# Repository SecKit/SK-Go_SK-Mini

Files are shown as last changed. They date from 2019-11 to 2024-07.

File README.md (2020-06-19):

# SK-Go² All-Metal CoreXY 3D Printer

Website

https://seckit3dp.design/

Join SecKit's FaceBook group for owner's discussion and latest update

https://www.facebook.com/groups/SecKitCoreXY3DP/

YouTube

https://www.youtube.com/channel/UCJUHiJfgDE5aeqbk4iZBPHA/videos

FaceBook Page

https://www.facebook.com/seckit.3dp

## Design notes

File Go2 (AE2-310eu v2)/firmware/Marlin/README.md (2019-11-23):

**How to re-flash firmware**

1. Put a corresponding binary into a TF card (micro SD). The 128MB TF comes with SKR v1.3 which must be **FAT16** formatted, other larger TF can be FAT32.
2. Rename the file as **firmware.bin**
3. Put the TF card into the slot on SKR v1.3
4. Reboot and it will re-flash. If success, the firmware.bin should have been renamed as FIRMWARE.CUR.

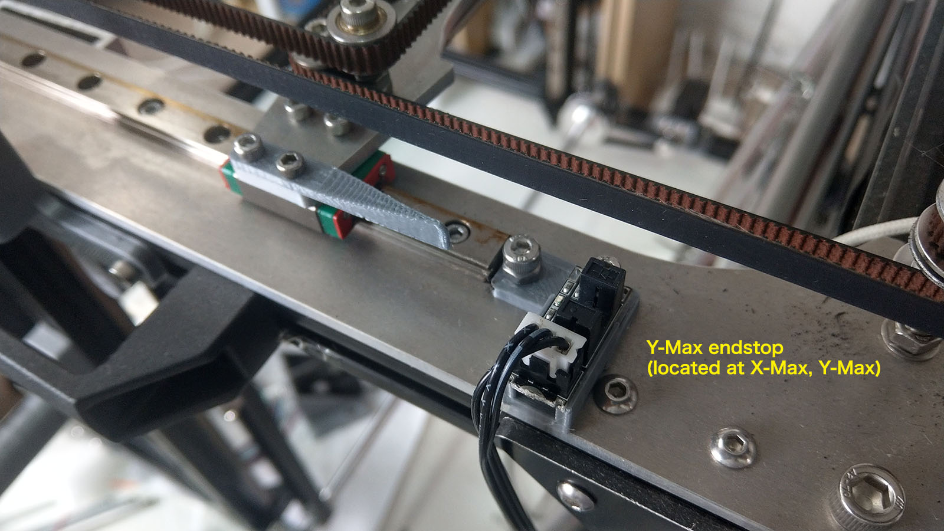
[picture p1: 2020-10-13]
Go2 (AE2-310eu v2)/printed parts STL/3. Optional/XY optical endstop mounts/Y-Max endstop.jpg

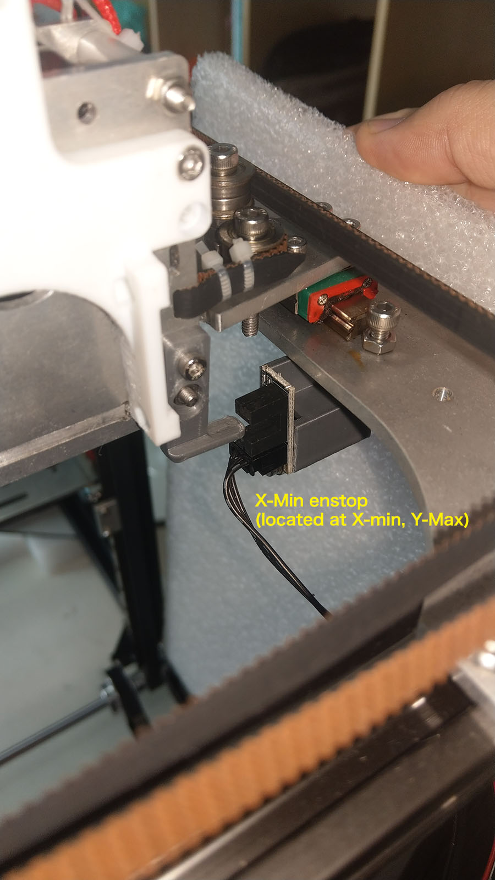
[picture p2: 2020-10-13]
Go2 (AE2-310eu v2)/printed parts STL/3. Optional/XY optical endstop mounts/X-min endstop 2.jpg

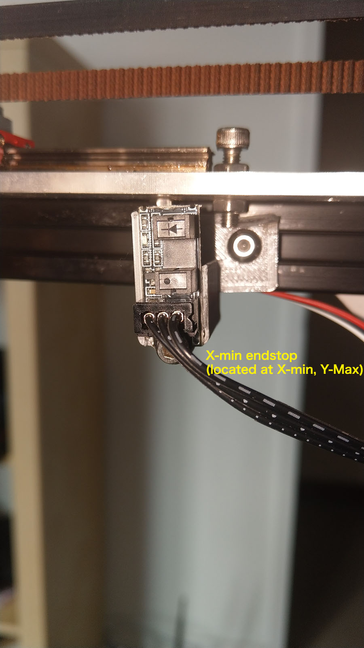
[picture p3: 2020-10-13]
Go2 (AE2-310eu v2)/printed parts STL/3. Optional/XY optical endstop mounts/X-min endstop 1.jpg

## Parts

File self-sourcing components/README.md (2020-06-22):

Self-sourcing components for SK-Go² Foundation & Barebones Kit.

|Category  |Item | #|Electrical req. |Mechanical req. |
|---|:---|-:|:---|:---|
|Power |Meanwell LRS-200-24 PSU | 1|200 or 350 watt, 24V output |4 holes on back panel (PS.)|
|Power |SSR DC-AC | 1|At least 10 amp AC |2 holes on back panel |
|Power |FS-101 fuse box and fuse | 1|6A for 110V. 3A for 220V. |1 hole on back panel |
|Power |Power switch | 1| | |
|Power |Power cord | 1|At least 0.75 mm^2 internal wire |150cm or longer |
|Control |BigTreeTech SKR v1.3. | 1|(or other control board) |4 holes on back panel |
|Control |BigTreeTech TMC2209 | 4|(or other drivers) | |
|Control |12864 LCD | 1|(optional) | |
|Control |JTAG cable for 12864 LCD, 80cm | 2|(optional) |80cm or longer |
|Stepper |NEMA17 1.8° stepper for XYZ | 3|Common NEMA 17 stepper | |
|Stepper |NEMA17 1.8° pancake stepper for E | 1|Common NEMA 17 pancake stepper |max 24mm tall (PPS.) |
|Extruder  |BMG or Hemera extruder | 1| | |
|Fan |4010 fan for driver cooling | 1|24V | |
|Fan |4020 blower for part cooling | 1|24V | |
|Sensor |Lerdge optical endstop, Z-min. | 1|5V | |
|Sensor |Filament runout sensor | 1|(optional) | |
|Accessory |PTFE tube 1.75mm, 80cm | 1| | |
|Accessory |Cable tie |20| | |
|Accessory |Cable management nylon sleeve, wrapper, etc.| 1| | |

PS. Pre-drilled holes are there on the ACM (Aluminum Composite Material) back panel but you can still drill customized holes easily.

PPS. For direct extrusion E stepper should be at most 24mm tall, or it cannot be inserted in between stock extruder plates.

*SecKit will not be responsible for your self-sourcing items.*

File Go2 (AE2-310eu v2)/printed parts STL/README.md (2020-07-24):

SK-Go² can still start it's initial print without these parts. Below are some workarounds if you don't have them printed.

**Assembly guide**

A ruler or caliper that keeps dimensions consistent will work. It's just a convenient tool and you can still complete the building without it.

**Cable pillar**

Temporarily hold wires/cables onto sticks.

**Driver cooling fan mount**

TMC drivers still work without a fan and they auto reduce working current if overheated.

**Part-cooling fan duct**

A desktop fan placed by the printer will work.

**X-min sensorless homing bumper**

It still homes without this bumper, just noisier.

**12864 Display cover**

The display still works without a cover.

**Filament sensor holder**

Temporarily turn sensor off in the display menu, or put a piece of filament in the sensor to emulate filament always exists.

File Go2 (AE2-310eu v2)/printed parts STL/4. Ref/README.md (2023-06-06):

The DXF file of a wider Go1/Go2 X plate.

License: CC BY-NC-SA 4.0

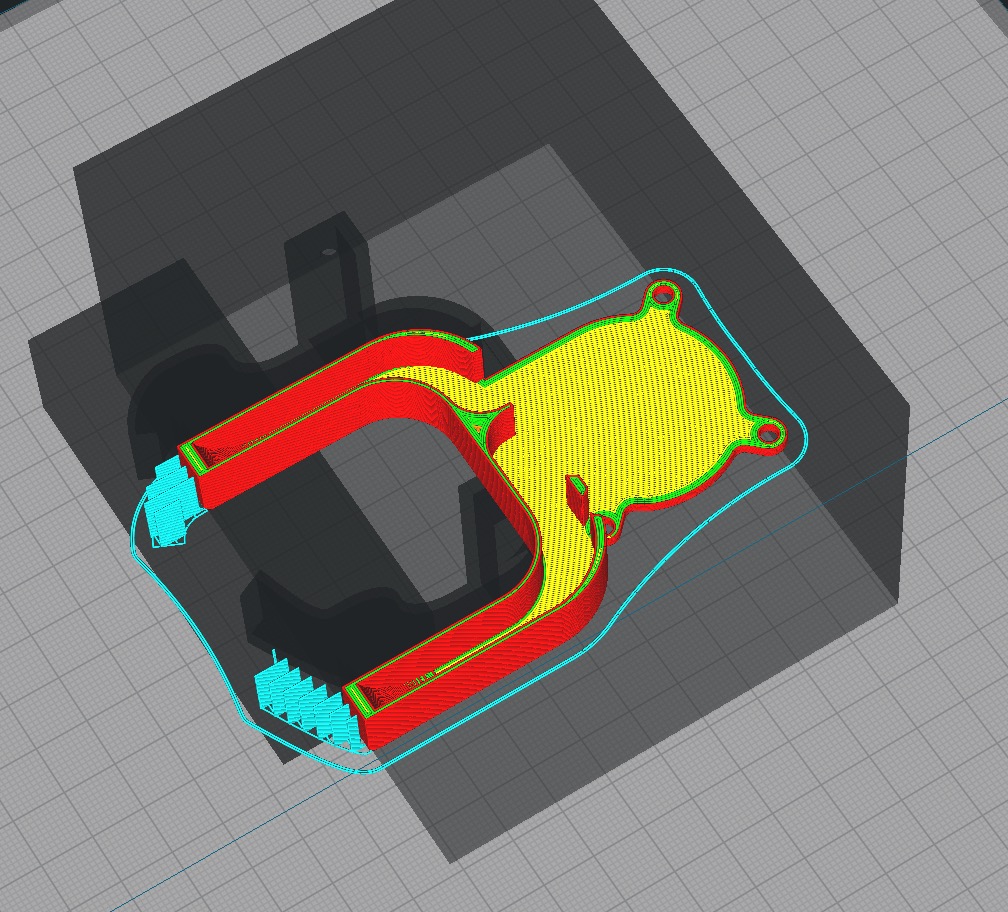
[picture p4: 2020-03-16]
Go2 (AE2-310eu v2)/printed parts STL/2. Recommended/4. Part-cooling fan duct/Direct.v2/pic1.jpg

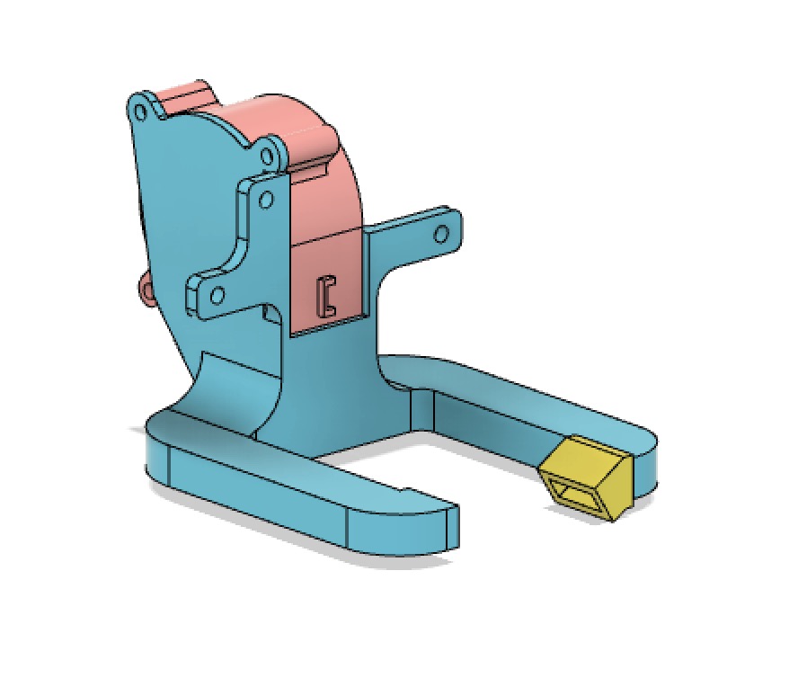
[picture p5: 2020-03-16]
Go2 (AE2-310eu v2)/printed parts STL/3. Optional/E3D Hemera fan duct/pic0.jpg

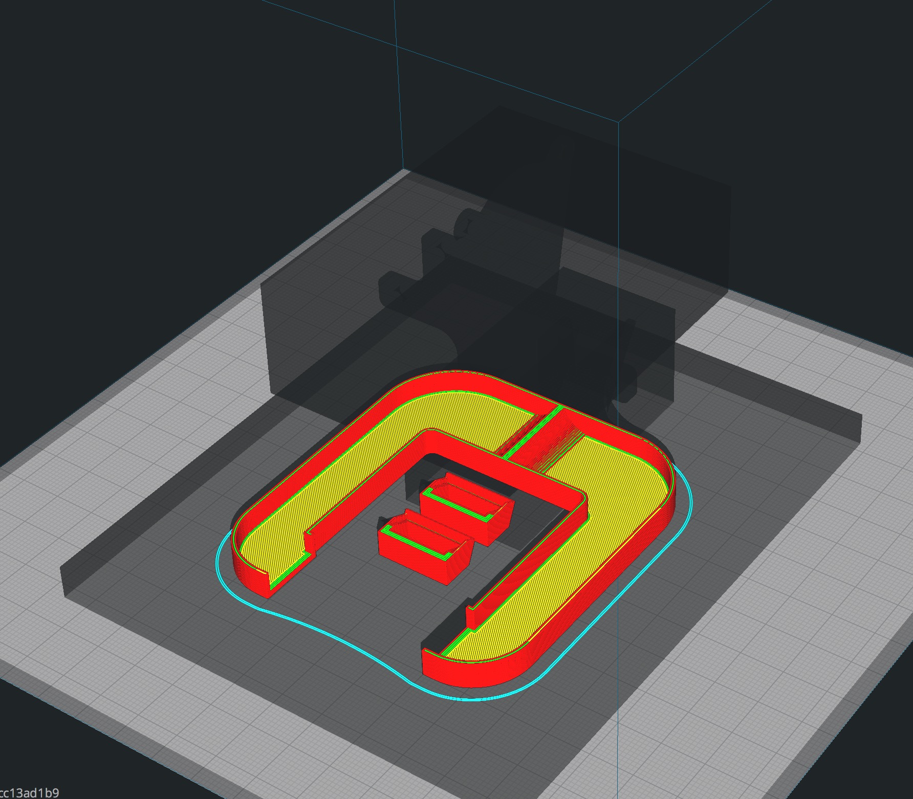
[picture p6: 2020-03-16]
Go2 (AE2-310eu v2)/printed parts STL/3. Optional/E3D Hemera fan duct/pic1.jpg

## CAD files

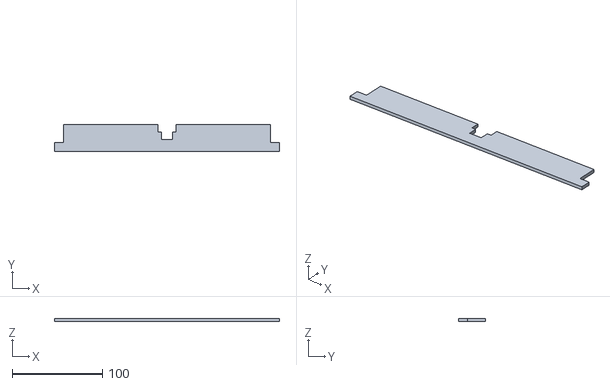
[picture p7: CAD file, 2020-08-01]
Go2 (AE2-310eu v2)/printed parts STL/2. Recommended/1. Assembly guide/SK-Go2 assembly guide - Setup A.stl
250.0 x 29.5 x 3.00

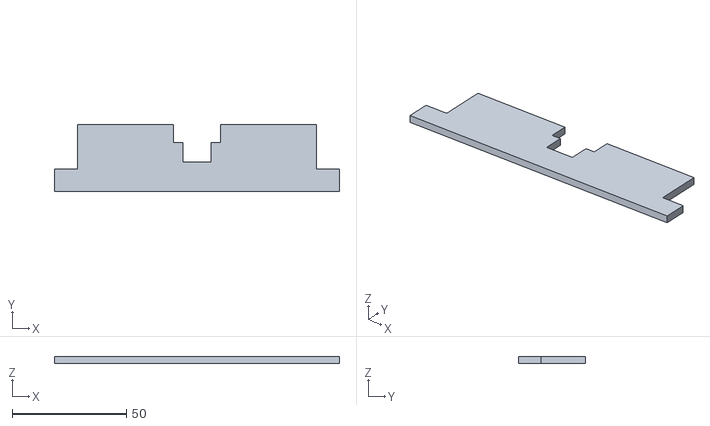
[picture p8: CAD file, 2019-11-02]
Go2 (AE2-310eu v2)/printed parts STL/2. Recommended/1. Assembly guide/SK-Mini assembly guide.stl
125.0 x 29.5 x 3.00

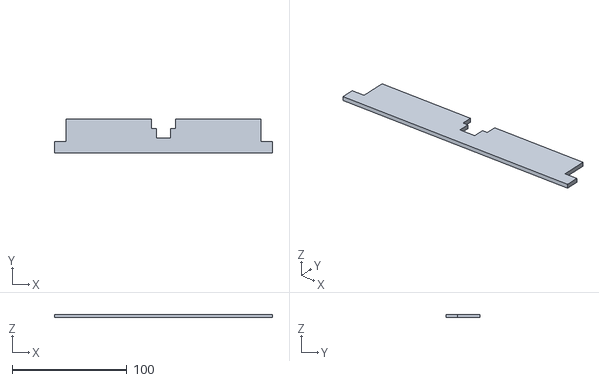
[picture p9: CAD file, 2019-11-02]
Go2 (AE2-310eu v2)/printed parts STL/2. Recommended/1. Assembly guide/SK-Go2 assembly guide - Setup B.stl
190.0 x 29.5 x 3.00

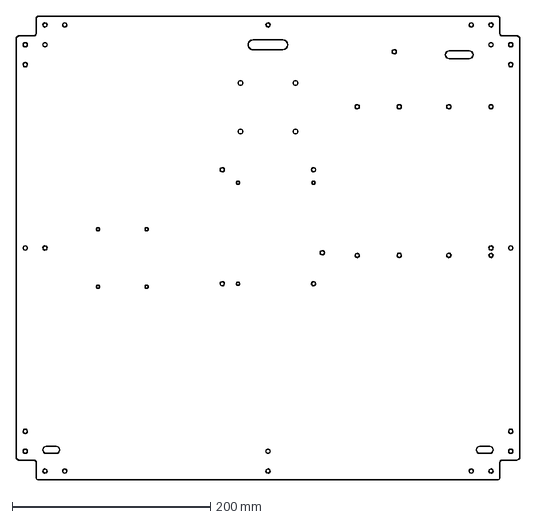
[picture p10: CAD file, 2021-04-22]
frame spec/SK-Go back panel Z350.dxf
507.9 x 468.0 mm

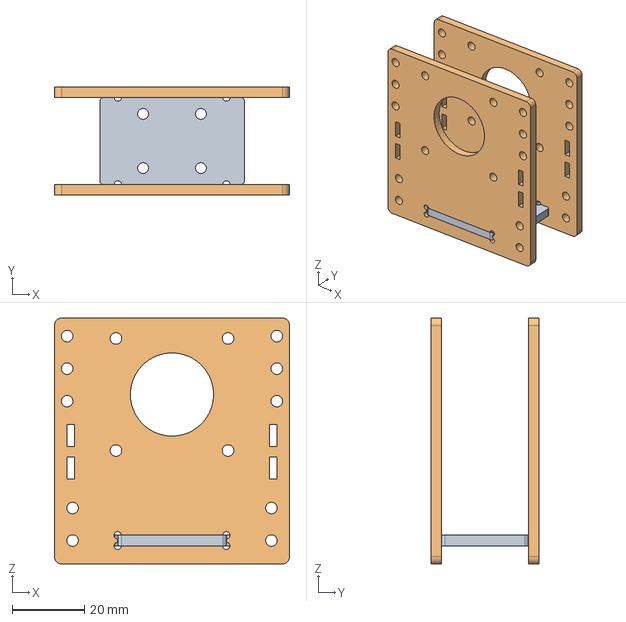
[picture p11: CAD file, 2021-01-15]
Go2 (AE2-310eu v2)/extruder carriage STEP file/SK-Go extruder carriage plates.step
65.0 x 30.0 x 68.0 mm

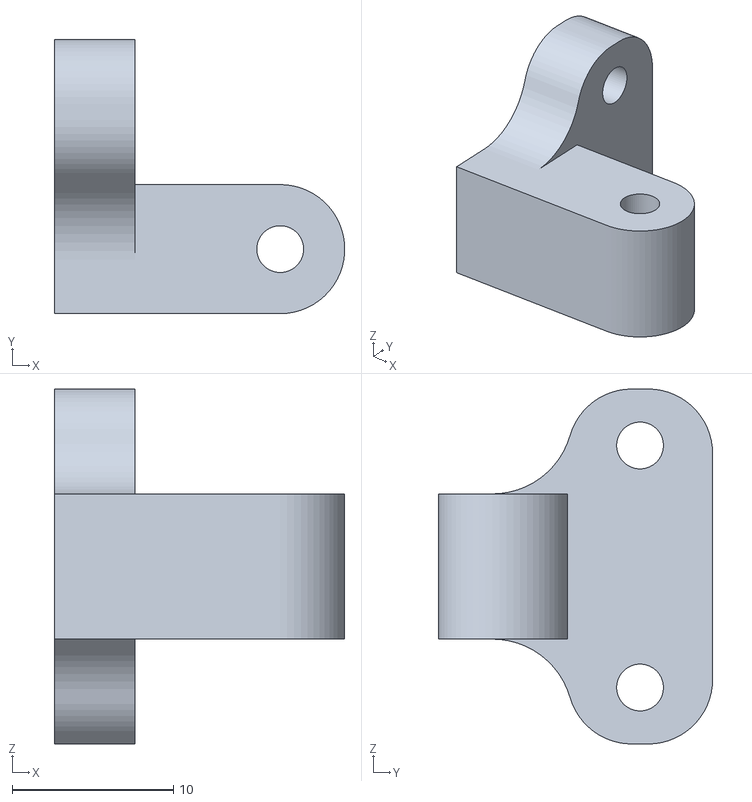
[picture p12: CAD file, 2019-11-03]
Go2 (AE2-310eu v2)/printed parts STL/1. Must/Z endstop mount/Mechanical endstop/Mechanical endstop mount by Michael Laws/SK-Go Z endstrop trigger mount by Michael Laws.stl
18.0 x 17.0 x 22.0

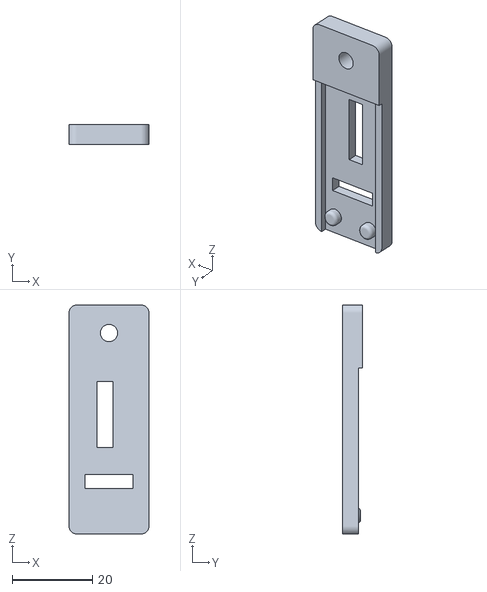
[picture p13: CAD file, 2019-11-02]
Go2 (AE2-310eu v2)/printed parts STL/1. Must/Z endstop mount/Mechanical endstop/Mechanical endstop mount/SK-Go Z endstop mount.stl
20.0 x 5.00 x 57.2

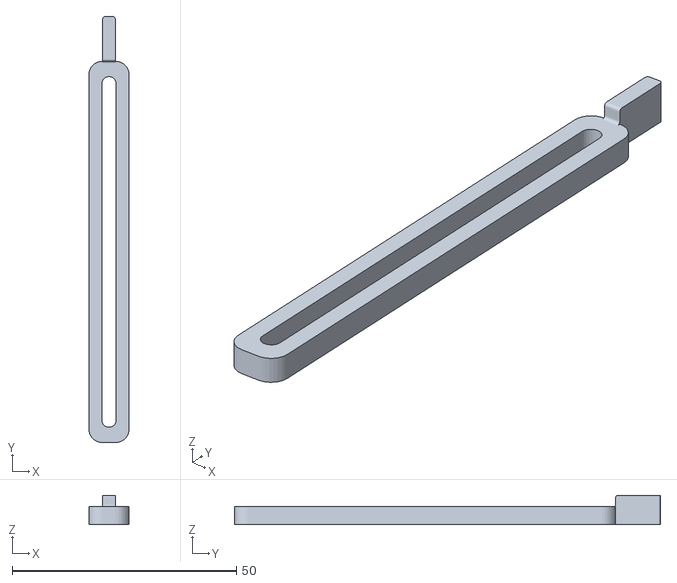
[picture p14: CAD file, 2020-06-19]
Go2 (AE2-310eu v2)/printed parts STL/1. Must/Z endstop mount/Optical endstop/SK-Go Z optical endstop trigger 95mm.stl
9.00 x 95.0 x 6.50

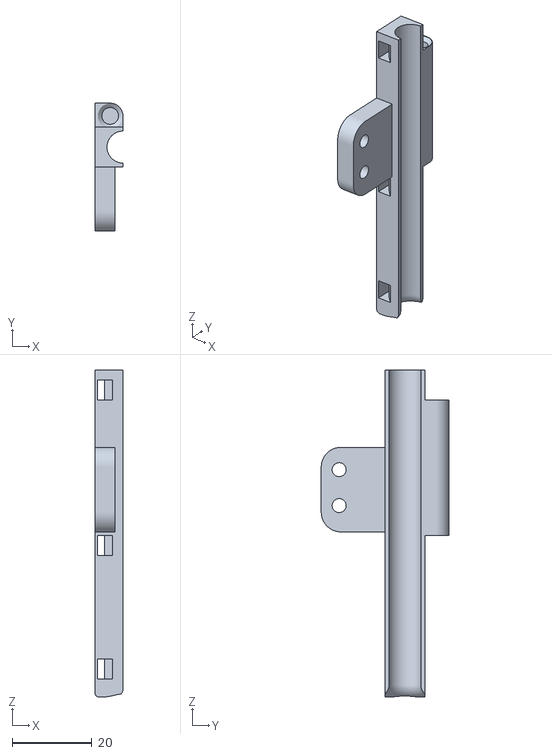
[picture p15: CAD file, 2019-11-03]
Go2 (AE2-310eu v2)/printed parts STL/2. Recommended/2. Cable pillar/SK-Go extruder cable holder by Michael Laws.stl
7.00 x 32.0 x 82.0

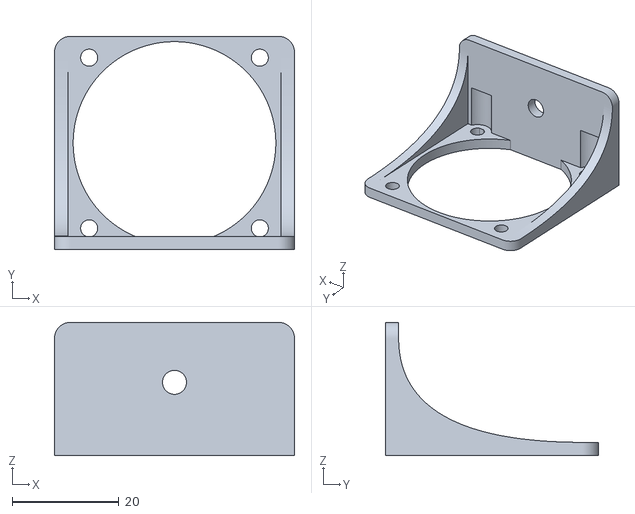
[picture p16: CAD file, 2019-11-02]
Go2 (AE2-310eu v2)/printed parts STL/2. Recommended/3. Driver cooling fan mount/SK-Go driver cooling fan mount.stl
45.0 x 40.0 x 25.0

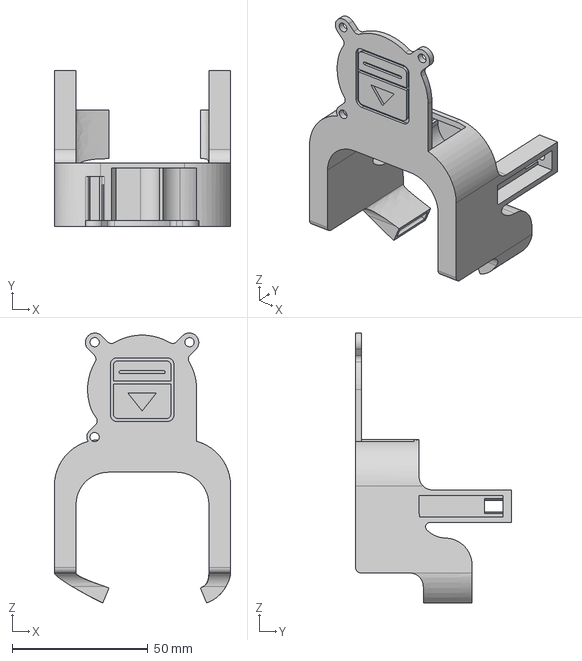
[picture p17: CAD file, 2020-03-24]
Go2 (AE2-310eu v2)/printed parts STL/2. Recommended/4. Part-cooling fan duct/Direct.v2/E3D V6 hotend/SK-Go fan duct.v2.direct.step
65.0 x 57.5 x 99.6 mm

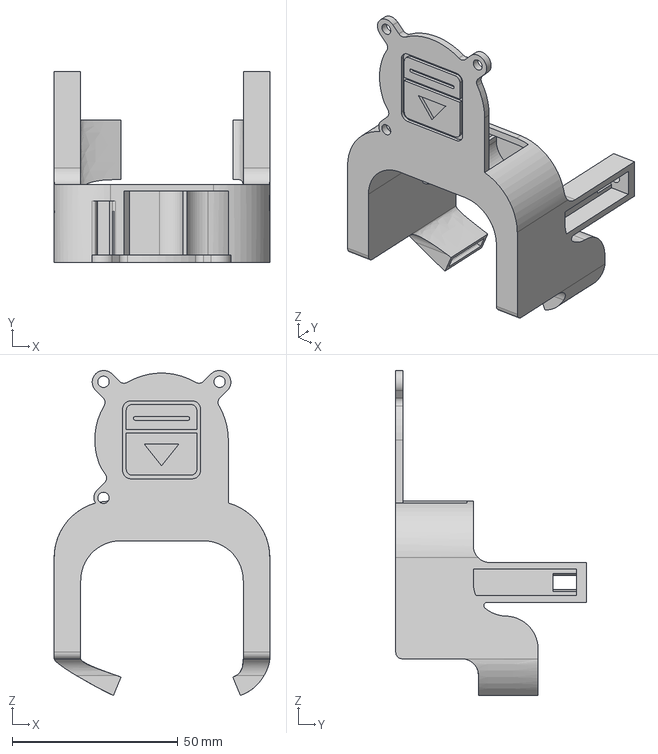
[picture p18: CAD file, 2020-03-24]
Go2 (AE2-310eu v2)/printed parts STL/2. Recommended/4. Part-cooling fan duct/Direct.v2/Mosquito hotend/SK-Go fan duct.v2.direct.mosquito.step
65.0 x 57.5 x 98.0 mm

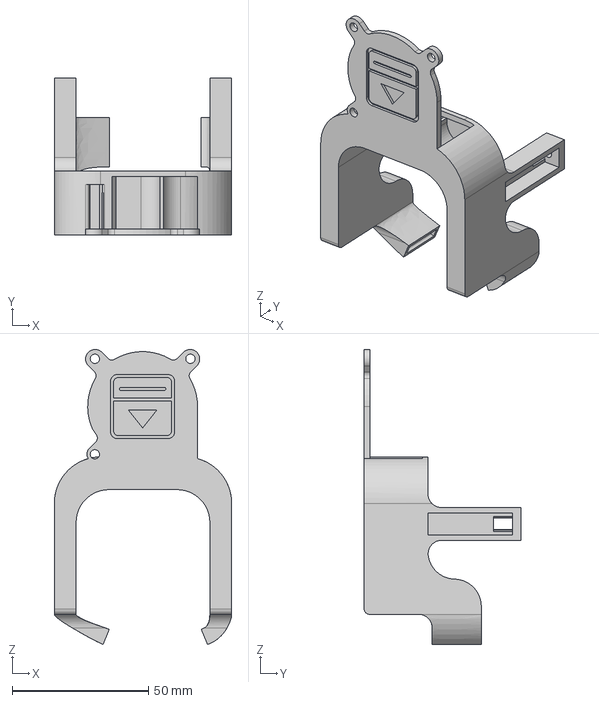
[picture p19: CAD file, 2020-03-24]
Go2 (AE2-310eu v2)/printed parts STL/2. Recommended/4. Part-cooling fan duct/Direct.v2/Volcano hotend/SK-Go fan duct.v2.direct.volcano.step
65.0 x 57.5 x 108.1 mm

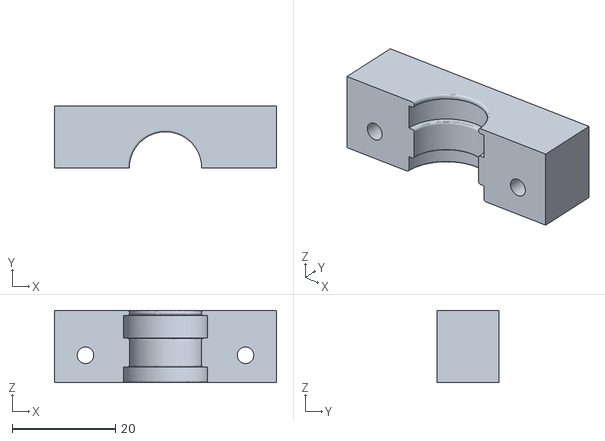
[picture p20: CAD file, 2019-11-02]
Go2 (AE2-310eu v2)/printed parts STL/2. Recommended/4. Part-cooling fan duct/Remote/E3D V6 hotend/SK-Go fan duct.remote.part B.stl
43.0 x 12.0 x 14.0

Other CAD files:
Go2 (AE2-310eu v2)/printed parts STL/2. Recommended/5. X-min sensorless homing bumper/SK-Go X-min sensorless homing bumper.stl
Go2 (AE2-310eu v2)/printed parts STL/2. Recommended/7. Filament sensor holder/SK-Go filament sensor holder by Michael Laws.stl
Go2 (AE2-310eu v2)/printed parts STL/2. Recommended/8. Spool pillar/SK-Go spool pillar.stl
Go2 (AE2-310eu v2)/printed parts STL/1. Must/Z endstop mount/Mechanical endstop/Mechanical endstop mount by Michael Laws/SK-Go Z endstop mount by Michael Laws.stl
Go2 (AE2-310eu v2)/printed parts STL/1. Must/Z endstop mount/Optical endstop/SK-Go Z optical switch base.stl
Go2 (AE2-310eu v2)/printed parts STL/2. Recommended/2. Cable pillar/SK-Go frame cable pillar.stl
Go2 (AE2-310eu v2)/printed parts STL/2. Recommended/4. Part-cooling fan duct/Direct.v2/E3D V6 hotend/SK-Go fan duct.v2.direct.stl
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

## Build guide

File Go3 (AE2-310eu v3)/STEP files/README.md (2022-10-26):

Slicing tips

Printed files are all non-structural components so a common PLA or PETG filament with 0.4mm nozzle and 0.2mm layer height will do. Use ABS/ASA if your printer is enclosed. For special slicing settings please refer to the README.md file and print orientation pictures in each STL directory.   

All designs in this directory and subdirectories are shared under [CC BY-NC-SA 4.0](https://creativecommons.org/licenses/by-nc-sa/4.0/)

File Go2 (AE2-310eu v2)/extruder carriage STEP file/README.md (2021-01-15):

STEP files of SecKit SK-Go extruder plates and carriage.

License: CC BY-NC-SA 4.0
https://creativecommons.org/licenses/by-nc-sa/4.0/

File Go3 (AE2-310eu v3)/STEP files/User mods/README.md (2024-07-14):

# Seckit SK-Go3 User Mods

Welcome to the User Mods section for the Seckit SK-Go3 3D printer! This repository is dedicated to sharing and showcasing user-created modifications and enhancements for the Seckit SK-Go3. Whether you're looking to improve the performance, functionality, or aesthetics of your printer, you'll find a variety of mods contributed by the community here.

The Seckit SK-Go3 is a versatile and high-performance 3D printer, and this repository aims to make it even better by providing a platform for users to share their mods. From printable upgrades to hardware enhancements, this is your go-to place for improving your Seckit SK-Go3.

# Mods

## Printable Mods

Printable mods are 3D models that can be printed and used to upgrade or enhance the Seckit SK-Go3. Examples include custom fan ducts, cable management solutions, and improved spool holders.

## Hardware Mods

Hardware mods involve adding or modifying physical components of the printer. These mods might require additional tools or parts.

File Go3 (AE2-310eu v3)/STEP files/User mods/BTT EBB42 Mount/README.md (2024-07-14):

# Bigtreetech EBB42 Mount

This mod enables the secure mounting of the Bigtreetech EBB42 to the back of a carbon fiber extruder mount, enhancing the functionality of your 3D printer. It is a modified mount for the x microswitch. You may need a different x/y finger.

## Parts Required

Bigtreetech EBB42
4x M3 heat inserts
Assorted M3 bolts (appropriate length for your setup)

## Assembly Instructions

# Prepare the Mount:

Insert the 4 M3 heat inserts into the designated slots on the EBB42 mount. Ensure they are properly seated.
Install the X microswitch. Ensure it is securely attached and properly aligned for correct functioning.

# Attach the EBB42 Mount

Attatch the mount to the back plate of the extruder. Depending on what setup you are using you will need different length bolts to match.

# Install the EBB42

Position the Bigtreetech EBB42 on the back of the new mount, aligning the mounting holes with the heat inserts over the installed X microswitch.
Ensure the screws are tightened appropriately to avoid damaging the components.

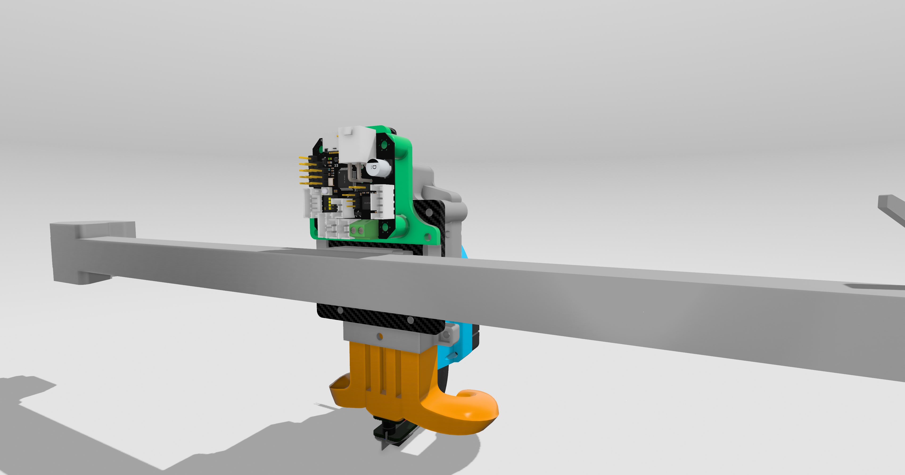
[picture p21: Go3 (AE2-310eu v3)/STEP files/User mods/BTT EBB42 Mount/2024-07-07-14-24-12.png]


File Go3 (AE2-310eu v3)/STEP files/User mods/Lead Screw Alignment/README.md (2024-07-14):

# Lead Screw Aligner

The Lead Screw Aligner is a simple yet effective tool designed to maintain the alignment of the lead screw in your 3D printer. By utilizing a 608RS bearing, this tool ensures the lead screw remains centered, reducing wobble and improving print quality.

# Parts Required

608RS bearing
Lead Screw Aligner (3D printed part)

## Assembly Instructions

Print the provided Lead Screw Aligner file using your 3D printer. Ensure that the dimensions are accurate and the print quality is high.

Insert the 608RS bearing into the designated slot in the Lead Screw Aligner. Ensure it fits snugly and is seated properly.

Slide the part over the top of the lead screw and snap into place over the extrusion. You can use t-nuts to secure in place but it is snug and will stay there without it.
Position the Lead Screw Aligner near the top of the lead screw and keep enough clearance between the bed bracket and the tool on your 3D printer. The bearing should keep the lead screw centered and free to rotate at all times.



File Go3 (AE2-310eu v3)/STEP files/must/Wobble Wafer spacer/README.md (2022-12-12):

Slicer settings

|Setting |Description |
|:---|:---|
|Quantity |1 |
|Wall thickness |2mm |
|Infill |100% |
|Support |None |

PLA/PETG, 0.4mm nozzle, 0.2mm layer height

Use ABS/ASA if printer is enclosed.

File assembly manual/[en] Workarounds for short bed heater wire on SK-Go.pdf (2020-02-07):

# Workarounds for short bed heater wire on SK-Go

2020/01/25

Web https://seckit3dp.design
FB https://facebook.com/seckit.3dp Email seckit.3dp@gmail.com

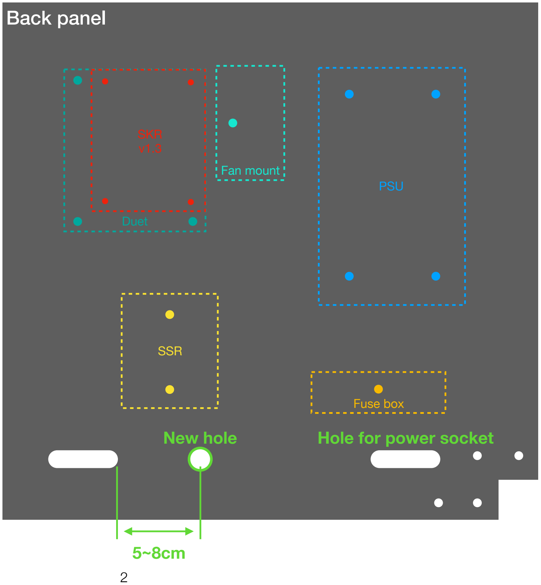
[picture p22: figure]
Back panel; PSU; Fuse box; SSR; Duet; SKR v1.3; Fan mount; New hole; Hole for power socket

## Method 1:

Follow the wiring diagram in Assembly Manual, but drill a new hole, or pass the wire to be connected to Line terminal through the hole for power socket.

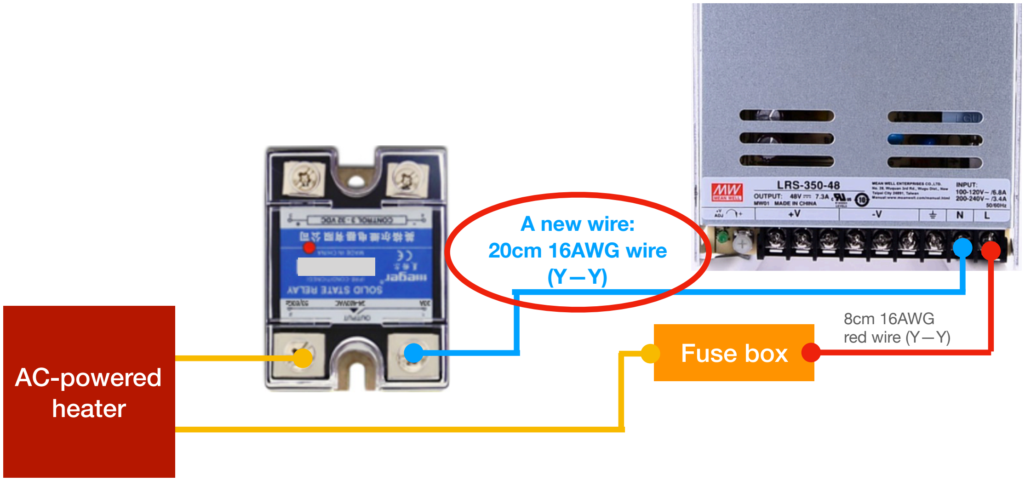
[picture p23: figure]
Fuse box; 8cm 16AWG red wire (Y—Y); AC-powered heater; A new wire: 20cm 16AWG wire (Y—Y)

3

## Method 2:

Use a new wire of 20cm 16AWG and follow the wiring diagram below

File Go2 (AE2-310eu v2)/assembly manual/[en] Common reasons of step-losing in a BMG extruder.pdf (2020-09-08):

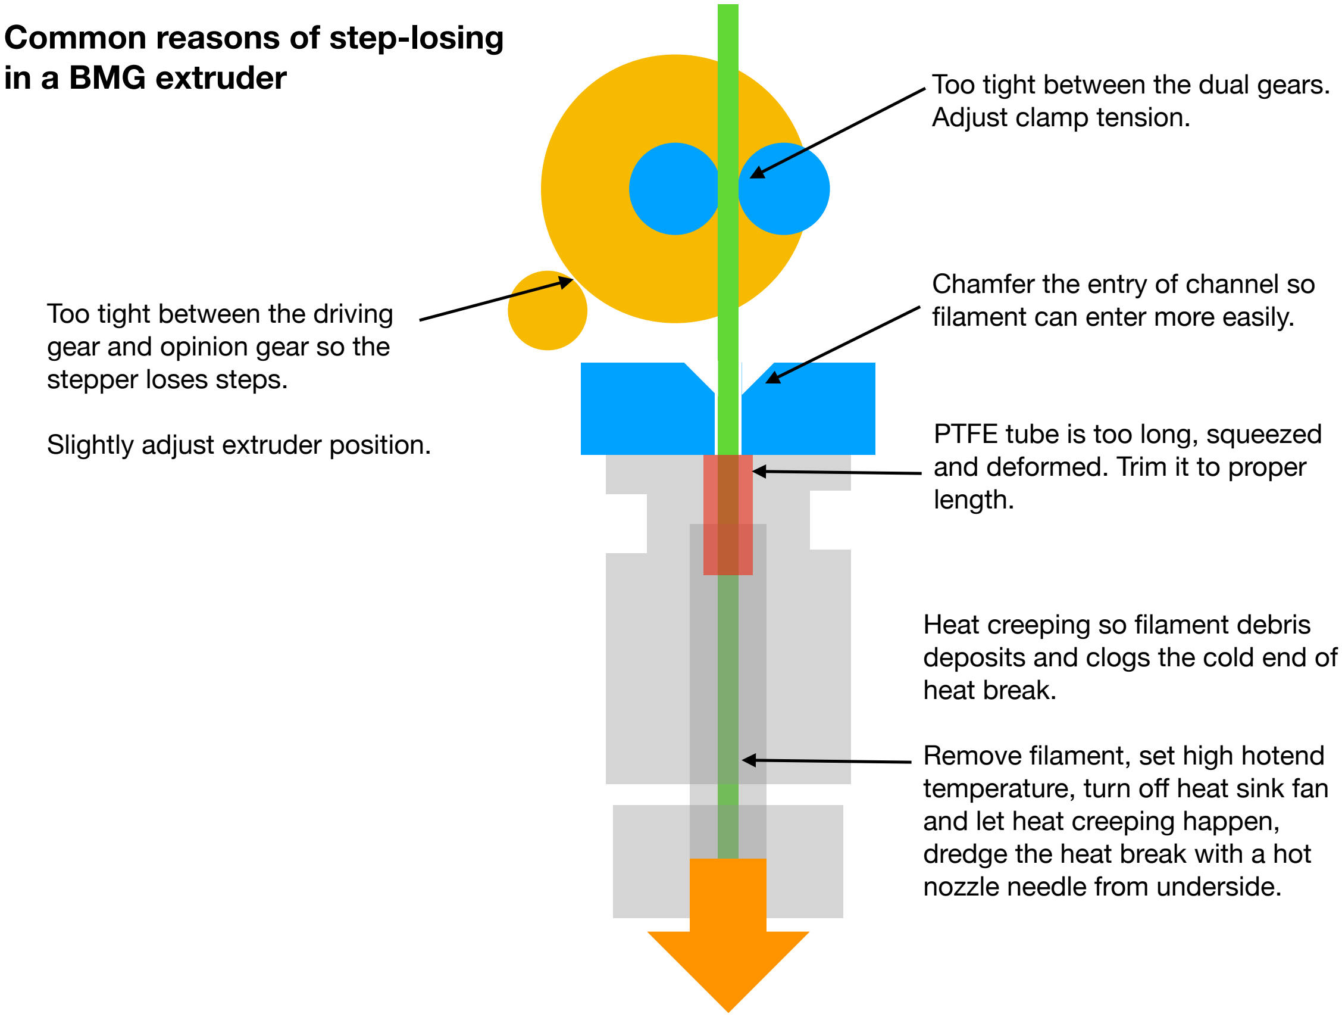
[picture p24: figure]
Too tight between the driving gear and opinion gear so the stepper loses steps.; Slightly adjust extruder position.; Too tight between the dual gears. Adjust clamp tension.; Chamfer the entry of channel so filament can enter more easily.; PTFE tube is too long, squeezed and deformed. Trim it to proper length.; Heat creeping so filament debris deposits and clogs the cold end of heat break.; Remove filament, set high hotend temperature, turn off heat sink fan and let heat creeping happen, dredge the heat break with a hot nozzle needle from underside.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

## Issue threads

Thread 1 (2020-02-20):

12864 display reset button wrong bottom height

MaKaNu, 2020-02-20:
My printed Reset Button from [https://github.com/SecKit/SK-Go_SK-Mini/blob/master/printed%20parts%20STL/2.%20Recommended/6.%2012864%20Display%20cover/12864%20display%20reset%20button.stl](url) has the wrong height to reach the display reset button in short distance. This left the button unstable. I measured the distance between reset button and display cover with ~5 mm if the bottom of the button in not about 2 mm rather around 4 to 4.5 mm it would be more stable.

MaKaNu, 2020-02-21:
I created two Versions that should work better: a short button and a long button

SecKit, 2020-02-21:
Hi @MaKaNu, thank you for reporting this issue. I just updated a new version of cover and button (3b5fd47) with these improvements:

- bolt hole alignment
- shorter and longer reset button
- add support between cover and PCB to prevent pressing cover and erroneously trigger reset button

MaKaNu, 2020-02-22:
Looking Great. I close the Issue.

Closed 2020-02-22.

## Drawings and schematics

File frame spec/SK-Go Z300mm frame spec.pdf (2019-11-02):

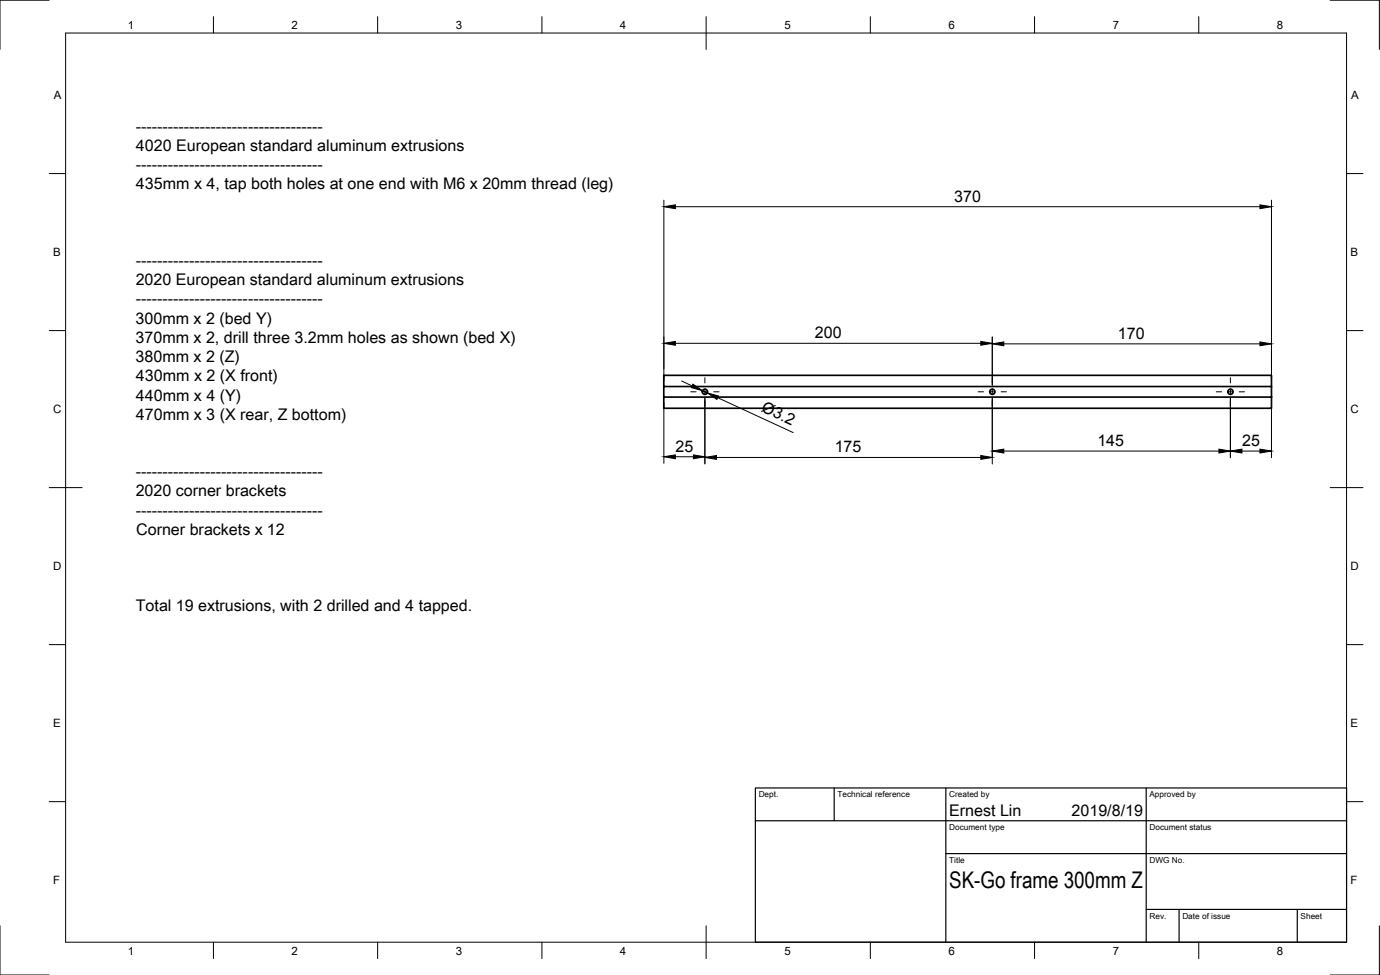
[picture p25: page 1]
----------------------------------- 300mm x 2 (bed Y); ----------------------------------- 2020 corner brackets; ----------------------------------- Corner brackets x 12

----------------------------------- 4020 European standard aluminum extrusions

----------------------------------- 435mm x 4, tap both holes at one end with M6 x 20mm thread (leg)

----------------------------------- 2020 European standard aluminum extrusions

370mm x 2, drill three 3.2mm holes as shown (bed X)
430mm x 2 (X front)
470mm x 3 (X rear, Z bottom)

Total 19 extrusions, with 2 drilled and 4 tapped.

Dept. | Technical reference | Created by Ernest Lin 2019/8/19 | Approved by

Document type | Document status

Title SK-Go frame 300mm Z | DWG No.

Rev. | Date of issue | Sheet

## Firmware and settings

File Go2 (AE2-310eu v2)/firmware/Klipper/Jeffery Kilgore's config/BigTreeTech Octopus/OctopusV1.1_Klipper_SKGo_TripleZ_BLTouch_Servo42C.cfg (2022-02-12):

[include kiauh_macros.cfg]
[mcu]
serial: /dev/serial/by-id/usb-Klipper_stm32f446xx_3F001100085053424E363420-if00

[display_status]

[virtual_sdcard]
path: ~/gcode_files

[printer]
kinematics: corexy
max_velocity: 400  
max_accel: 3000    			#Max 4000
max_accel_to_decel: 2500
max_z_velocity: 8 			#Max 15 for 12V TMC Drivers, can increase for 24V
max_z_accel: 200
square_corner_velocity: 6.0

[mcu rpi]
serial: /tmp/klipper_host_mcu

[adxl345]
cs_pin: rpi:None

[resonance_tester]
accel_chip: adxl345
probe_points:
    175,175,20  # an example

[temperature_sensor raspberry_pi]
sensor_type: temperature_host
min_temp: 10
max_temp: 100

[bltouch]
sensor_pin: ^PB7
control_pin: PB6
pin_move_time: 0.4
stow_on_each_sample: True
probe_with_touch_mode: True #Needed for BLTouch V3.0 / V3.1
x_offset: 0
y_offset: 30
#z_offset: 2.250
speed: 5
samples: 3
sample_retract_dist: 3
samples_result: average

[safe_z_home]
home_xy_position: 160,150 # Change coordinates to the center of your print bed
speed: 100
z_hop: 10                 # Move up 10mm
z_hop_speed: 7.5

#####################################################################
# 	X/Y Stepper Settings
#####################################################################

[stepper_x]
#MKS Servo42C Motors
step_pin: PG0
dir_pin: !PG1
enable_pin: !PF15
rotation_distance: 32 # was 32 default @ 16 microsteps
microsteps: 16 #16 Default
full_steps_per_rotation: 200  #set to 400 for 0.9 degree stepper - default
endstop_pin: PG6
position_min: -1
position_endstop: -1
position_max: 325 # Reset to 325 when cable chain / x carriage is fixed
homing_speed: 60  #Max 100
homing_retract_dist: 5
#homing_positive_dir: true
#step_pulse_duration: 0.000002000
#   The minimum time between the step pulse signal edge and the
#   following "unstep" signal edge. This is also used to set the
#   minimum time between a step pulse and a direction change signal.
#   The default is 0.000000100 (100ns) for TMC steppers that are
#   configured in UART or SPI mode, and the default is 0.000002 (which
#   is 2us) for all other steppers.



## X Stepper on MOTOR0(B Motor)
[stepper_y]
#MKS Servo42C Motors
step_pin: PF13
dir_pin: !PF12
enable_pin: !PF14
rotation_distance: 32 #was 32 default
microsteps: 16 # 16 default
full_steps_per_rotation: 200  #set to 400 for 0.9 degree stepper -default
endstop_pin: PG9 #pg9
position_min: 0
position_endstop: 0
position_max: 325 #reset to 355 when cable chain is fixed
homing_speed: 60   #Max 100
homing_retract_dist: 5
#homing_positive_dir: true
#step_pulse_duration: 0.000002000
#   The minimum time between the step pulse signal edge and the
#   following "unstep" signal edge. This is also used to set the
#   minimum time between a step pulse and a direction change signal.
#   The default is 0.000000100 (100ns) for TMC steppers that are
#   configured in UART or SPI mode, and the default is 0.000002 (which
#   is 2us) for all other steppers.
 
#####################################################################
# 	Z Stepper Settings
#####################################################################

## Z0 Stepper - Front Left on MOTOR2_1
[stepper_z]
step_pin: PF11
dir_pin: PG3
enable_pin: !PG5
rotation_distance: 1
#gear_ratio: 20:1
microsteps: 128
endstop_pin: probe:z_virtual_endstop
#position_endstop: 0
position_max: 340
position_min: -1.5
homing_speed: 4
second_homing_speed: 2
homing_retract_dist: 5

##	Make sure to update below for your relevant driver (2208 or 2209)
[tmc2209 stepper_z]
uart_pin: PC6
interpolate: false
run_current: 1.00
hold_current: 0.4
sense_resistor: 0.110
stealthchop_threshold: 0

##	Z1 Stepper - Rear Left on MOTOR3
[stepper_z1]
step_pin: PG4
dir_pin: PC1
enable_pin: !PA0
rotation_distance: 1
#gear_ratio: 20:1
microsteps: 128

##	Make sure to update below for your relevant driver (2208 or 2209)
[tmc2209 stepper_z1]
uart_pin: PC7
interpolate: false
run_current: 1.00
hold_current: 0.4
sense_resistor: 0.110
stealthchop_threshold: 0

##	Z2 Stepper - Rear Right on MOTOR4
[stepper_z2]
step_pin: PF9
dir_pin: !PF10
enable_pin: !PG2
rotation_distance: 1
#gear_ratio: 20:1
microsteps: 128

##	Make sure to update below for your relevant driver (2208 or 2209)
[tmc2209 stepper_z2]
uart_pin: PF2
interpolate: false
run_current: 1.00
hold_current: 0.4
sense_resistor: 0.110
stealthchop_threshold: 0

#####################################################################
# 	Extruder
#####################################################################

#	E0 on MOTOR6
[extruder]
step_pin: PE2
dir_pin: PE3
enable_pin: !PD4
##	Update value below when you perform extruder calibration
##	If you ask for 100mm of filament, but in reality it is 98mm:
##	rotation_distance = <previous_rotation_distance> * <actual_extrude_distance> / 100
##  22.6789511 is a good starting point
rotation_distance: 5.7	#Bondtech 5mm Drive Gears
#gear_ratio: 50:17				#BMG Gear Ratio
microsteps: 128
full_steps_per_rotation: 200	#200 for 1.8 degree, 400 for 0.9 degree
nozzle_diameter: 0.400
filament_diameter: 1.75
heater_pin: PA2
##	Validate the following thermistor type to make sure it is correct
sensor_type: ATC Semitec 104GT-2
sensor_pin: PF4
min_temp: 0
max_temp: 305
max_power: 1.0
min_extrude_temp: 160
#control = pid
#pid_kp = 26.213
#pid_ki = 1.304
#pid_kd = 131.721
##	Try to keep pressure_advance below 1.0
pressure_advance: 0.06
##	Default is 0.040, leave stock
pressure_advance_smooth_time: 0.060
max_extrude_only_distance: 100

##	E0 on MOTOR6
##	Make sure to update below for your relevant driver (2208 or 2209)
[tmc2208 extruder]
uart_pin: PE1
interpolate: false
run_current: 0.65
hold_current: 0.4
sense_resistor: 0.110
stealthchop_threshold: 0


#####################################################################
# 	Bed Heater
#####################################################################

[heater_bed]
##	SSR Pin - BED_OUT
heater_pin: PA1
sensor_type: Generic 3950
sensor_pin: PF3
##	Adjust Max Power so your heater doesn't warp your bed
max_power: 0.90
min_temp: 0
max_temp: 120
#control: pid
#pid_kp: 58.437
#pid_ki: 2.347
#pid_kd: 363.769

#####################################################################
# 	Fan Control
#####################################################################

[fan]
##	Print Cooling Fan - CNC_FAN0
pin: PA8
kick_start_time: 0.5
off_below: 0.10

[heater_fan hotend_fan]
##	Hotend Fan - CNC_FAN1
pin: PE5
max_power: 1.0
kick_start_time: 1.0
heater: extruder
heater_temp: 50.0
##	If you are experiencing back flow, you can reduce fan_speed
fan_speed: 1.0

[controller_fan MCU_controller_fan]
pin: PD12
max_power: 0.45
shutdown_speed: 0
kick_start_time: 0.5
idle_timeout: 30
idle_speed: 0.40
stepper: stepper_z, stepper_y, stepper_x, stepper_z2, stepper_z1, extruder

#####################################################################
# 	LED Control
#####################################################################

#[output_pin caselight]
# Chamber Lighting - HE1 Connector (Optional)
#pin: PA3
#pwm:true
#shutdown_value: 0
#value:1
#cycle_time: 0.01

#####################################################################
# 	Homing and Gantry Adjustment Routines
#####################################################################

[idle_timeout]
timeout: 600

[bed_mesh]
speed: 75
horizontal_move_z: 5
mesh_min: 10, 31
mesh_max: 315, 290
probe_count: 5,5
fade_start: 1
fade_end: 10
fade_target: 0

[z_tilt]
z_positions:
	-10, 22.5
	-10, 277
    333, 155
points:
	10,1
	10, 230
    315, 115 #reset to 345, 10 when cable chain is fixed
speed: 100
horizontal_move_z: 10
retries: 5
retry_tolerance: 0.02

[force_move]
enable_force_move: True #   Set to true to enable FORCE_MOVE and SET_KINEMATIC_POSITION

[input_shaper]

########################################
# EXP1 / EXP2 (display) pins
########################################

[board_pins]
aliases:
    # EXP1 header
    EXP1_1=PE8, EXP1_2=PE7,
    EXP1_3=PE9, EXP1_4=PE10,
    EXP1_5=PE12, EXP1_6=PE13,    # Slot in the socket on this side
    EXP1_7=PE14, EXP1_8=PE15,
    EXP1_9=<GND>, EXP1_10=<5V>,

    # EXP2 header
    EXP2_1=PA6, EXP2_2=PA5,
    EXP2_3=PB1, EXP2_4=PA4,
    EXP2_5=PB2, EXP2_6=PA7,      # Slot in the socket on this side
    EXP2_7=PC15, EXP2_8=<RST>,
    EXP2_9=<GND>, EXP2_10=<5V>

#####################################################################
# 	Displays
#####################################################################

## 	Uncomment the display that you have
#--------------------------------------------------------------------

;[gcode_arcs]
;resolution: 0.1

#[display]
##	RepRapDiscount 128x64 Full Graphic Smart Controller
#lcd_type: st7920
#cs_pin: EXP1_4
#sclk_pin: EXP1_5
#sid_pin: EXP1_3
#menu_timeout: 40
#encoder_pins: ^EXP2_5, ^EXP2_3
#click_pin: ^!EXP1_2

#[output_pin beeper]
#pin: EXP1_1

#--------------------------------------------------------------------
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

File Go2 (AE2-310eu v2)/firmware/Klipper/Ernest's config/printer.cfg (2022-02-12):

[printer]
kinematics: corexy
max_velocity: 500
max_accel: 2000
#max_z_velocity: 7.5    # Belted-Z
max_z_velocity: 20      # lead screw
max_z_accel: 50
square_corner_velocity: 15.0

[mcu]
baud: 250000
restart_method: command
serial: /dev/ttyACM0
#serial: /dev/serial/by-id/usb-marlinfw.org_Marlin_USB_Device_0600D006AF390C415BE90356F50020C2-if00


[stepper_x]
step_pin: P2.2
dir_pin: P2.6
enable_pin: !P2.1
step_distance: .005
position_min: -15
position_max: 305
endstop_pin: P1.29
position_endstop: -15
homing_positive_dir:false
homing_speed: 60
homing_retract_dist: 0

[stepper_y]
step_pin: P0.19
dir_pin: P0.20
enable_pin: !P2.8
step_distance: .005
position_min: -15
position_max: 300
endstop_pin: P1.26
position_endstop: 300
homing_positive_dir:true
homing_speed: 60
homing_retract_dist: 0

[stepper_z]
step_pin: P0.22
enable_pin: !P0.21
#dir_pin: !P2.11            # Belted-Z
#step_distance: 0.0003125   # Belted-Z
dir_pin: P2.11              # lead screw
step_distance: 0.0025       # lead screw
position_min: 0
position_max: 250
endstop_pin: P1.25
position_endstop: 0
homing_positive_dir:false
#homing_speed: 7.5          # Belted-Z
homing_speed: 20            # lead screw
homing_retract_dist:2

[extruder]
step_pin: P2.13
dir_pin: !P0.11
enable_pin: !P2.12
step_distance: .00255
nozzle_diameter: 0.400
filament_diameter: 1.750
heater_pin: P2.7
sensor_type: ATC Semitec 104GT-2
sensor_pin: P0.24
control: pid
pid_Kp: 15.99
pid_Ki: 1.02
pid_Kd: 62.42
min_temp: 0
max_temp: 300
pressure_advance: 0.11
max_extrude_cross_section: 50.0

[tmc2209 stepper_x]
uart_pin: P1.17
microsteps: 16
run_current: 0.7
hold_current: 0.500
stealthchop_threshold: 0
interpolate: true
#diag_pin: P1.29
#driver_SGTHRS: 140

[tmc2209 stepper_y]
uart_pin: P1.15
microsteps: 16
run_current: 0.7
hold_current: 0.500
stealthchop_threshold: 0
interpolate: true
#diag_pin: P1.27
#driver_SGTHRS: 120

[tmc2209 stepper_z]
uart_pin: P1.10
microsteps: 16
run_current: 0.800
hold_current: 0.600
stealthchop_threshold: 0
interpolate: true

[tmc2209 extruder]
uart_pin: P1.8
microsteps: 16
run_current: 0.6
hold_current: 0.6
stealthchop_threshold: 0
interpolate: true

[heater_bed]
heater_pin: P2.5
sensor_type: Generic 3950
sensor_pin: P0.23
#control: watermark
min_temp: 0
max_temp: 130
control: pid
#pid_Kp: 50.07      # 3mm bed
#pid_Ki: 5.74       # 3mm bed
#pid_Kd: 291.36     # 3mm bed
pid_Kp: 64.074      # 8mm bed
pid_Ki: 1.662       # 8mm bed
pid_Kd: 617.51      # 8mm bed

[fan]
pin: P2.3

[heater_fan my_nozzle_fan]
pin:P2.4
max_power:1
#shutdown_speed:
#cycle_time:
#hardware_pwm:
#kick_start_time:
#   See the "fan" section in example.cfg for a description of the
#   above parameters.
#heater: extruder
#   Name of the config section defining the heater that this fan is
#   associated with. If a comma separated list of heater names is
#   provided here, then the fan will be enabled when any of the given
#   heaters are enabled. The default is "extruder".
#heater_temp: 50.0
#   A temperature (in Celsius) that the heater must drop below before
#   the fan is disabled. The default is 50 Celsius.
fan_speed: 0.8


[display]
lcd_type: st7920
cs_pin: PA3
sclk_pin: PA1
sid_pin: PC1
encoder_pins: ^PD2, ^PD3
click_pin: ^!PC0

#[probe]
#pin: P1.25
#set_output_mode:
#x_offset:-18
#y_offset:+12
#z_offset:1.5
#speed:5
#samples:1

[display]
lcd_type: st7920
cs_pin: P1.19
sclk_pin: P1.21
sid_pin: P1.23
encoder_pins: ^P1.18, ^P1.20
click_pin: !P0.28

[homing_override]
gcode:
    G28 Y0
    G28 X0
    G28 Z0



#[bed_mesh]
#speed: 80
#horizontal_move_z: 5
#mesh_min: 50,50
#mesh_max: 250,250
#probe_count: 6,6

#[safe_z_home]
#home_xy_position: 150,150
#z_hop: 5.0

[gcode_macro END_PRINT]
gcode:
    M104 S0
    M140 S0
    G91 ; relative position
    G1 Z10 F450
    ;Retract the filament
    G92 E1
    G1 E-1 F300
    G90 ; abs position
    G1 X10 Y280 F6000
    M84

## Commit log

2019-11-03 fix scale problem
    [SK-Go Z endstop mount by Michael Laws.stl, SK-Go Z endstrop trigger mount by Michael Laws.stl, SK-Go extruder cable holder by Michael Laws.stl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]
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2019-11-05 add compiled firmware binary for reversed stepper direction
2019-11-09 A printed tensioner with gap left for shorter 976mm close-loop Z belt only. No need for 1000mm belt.
    [SK-Go Z printed belt tensioner.stl]
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2019-11-13 Use 7 bolts and nuts instead of 6. This is a typo due to manual didn't keep up with design update.
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2019-11-13 Revert "P.26 in assembly manual: add instruction of T-nut M6 of levers."
    This reverts commit b6fbae50c510875ebd6d260a1140ec1920d0c352.
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2019-11-13 add p.74 in Assembly Manual. Fixate wires.
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2019-11-17 expand bolt holes into slots to adapt errors at display PCB
    [12864 display cover.stl]
2019-11-19 add manual for loosen connectors at power socket module
2019-11-23 add 12864 display dial
    [12864 display dial.stl]
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2019-11-30 Re-organize the priority of printed parts
    [12864 display cover.stl, 12864 display dial.stl, 12864 display reset botton.stl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]
2019-11-30 Workarounds of working without printed parts
2019-12-04 add Z optical endstop cap
    [Z optical endstop cap.stl]
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2019-12-04 correct typo in filename
    [12864 display reset button.stl]
2019-12-04 add display cover with slope
    [12864 display cover with slope.stl, 12864 display dial.stl, 12864 display reset button.stl]
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2019-12-14 re-organize location of printed parts and add Z optical endstop cap
    [SK-Go Z endstop mount.stl, SK-Go Z optical endstop trigger 55mm.stl, SK-Go Z optical endstop trigger 65mm.stl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]
2019-12-14 remove all files under directory of deprecated code base
    [Configuration.h, Configuration_adv.h]
2019-12-14 re-organize location in directory
    [Z optical endstop cap.stl]
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2020-01-01 add initial version of Hemera adaptor
    [E3D Hemera adaptor.stl]
2020-01-01 add chamfer to Hemera adaptor
    [E3D Hemera adaptor.stl]
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2020-01-22 add instructions of filament runout sensor and fix typo.
2020-01-23 Assembly Manual v1.22: swap wire sequence for optical endstop
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2020-01-24 add extruder plate mockup
    [extruder plate mockup.stl]
2020-01-24 bug fix: thermistor for BMG and hybrid threshold.
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2020-02-04 optical endstop trigger stick: make the protrusion higher and more visible
    [SK-Go Z optical endstop trigger 70mm.stl]
2020-02-07 Workaround of wiring for shorter wires on bed heater.
2020-02-07 Assembly Manual v1.30: add TMC2209 sensitivity value, and a link to workaround for shorter wires of heat bed shipped in Jan/Feb 2020.
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2020-02-15 remove all files under "deprecated code base"
    [Configuration.h, Configuration_adv.h]
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2020-02-21 Redesign 12864 cover to align PCB bolt holes better. Add a shorter button of the same height with cover surface. Also add another longer button.
    [12864 display cover.stl, 12864 display reset button.longer.stl, 12864 display reset button.stl]
2020-02-24 add an opening at the side of cover for SD card slot
    [12864 display cover.stl]
2020-03-16 add Hemera fan duct
    [Hemera fan duct nozzle.stl, Hemera fan duct.stl]
2020-03-16 add SK-Go fan duct v2 and print guide
    [SK-Go fan duct.v2.direct.stl, SK-Go fan duct.v2.direct.volcano.stl]
2020-03-17 add Mosquito hotend for SK-Go fan duct v2
    [SK-Go fan duct.v2.direct.mosquito.stl]
2020-03-23 Extend both beams for 0.5mm to prevent collision with extruder.
    [SK-Go fan duct.v2.direct.mosquito.stl, SK-Go fan duct.v2.direct.stl, SK-Go fan duct.v2.direct.volcano.stl]
2020-03-24 Add step files and SecKit logo for fan ducts.
    [SK-Go fan duct.v2.direct.mosquito.step, SK-Go fan duct.v2.direct.step, SK-Go fan duct.v2.direct.volcano.step]
2020-03-24 add SecKit logo onto fan duct STLs
    [SK-Go fan duct.v2.direct.mosquito.stl, SK-Go fan duct.v2.direct.stl, SK-Go fan duct.v2.direct.volcano.stl]
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2020-06-19 Make Z optical endstop trigger thicker for easier to block IR.
    [SK-Go Z optical endstop trigger 70mm.stl, Z optical endstop trigger 95mm for inverted bed support.stl]
2020-06-20 add Ravindra Karonde's Duet2 config files
    [config.g, homeall.g, homex.g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]
2020-06-21 Updated for RRF3 (depricated commands and order requirement)
    [config.g]
2020-06-21 Added comment about PID tuning
    [config.g]
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2020-06-29 rename the old v1 fan duct directory as z_deprecated to prevent misuse.
    [SK-Go fan duct.direct.stl, SK-Go fan duct.direct.volcano.stl]
2020-07-13 Move longer 95mm optical endstop trigger to the Must directory, and move the shorter 70mm trigger to the Optional directory.
    [SK-Go Z optical endstop trigger 70mm.stl, SK-Go Z optical endstop trigger 95mm.stl]
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2020-07-28 add STL of extruder plate for 28mm pancake extruder stepper.
    [Extruder plate for 28mm pancake stepper.stl]
2020-07-29 bug fix for STL of extruder plate for 28mm pancake stepper.
    [Extruder plate for 28mm pancake stepper.stl]
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2020-07-30 Add STLs of XY mechanical endstops.
    [X endstop mount.stl, X endstop trigger.stl, Y endstop mount - position B.stl]
2020-07-30 SK-Go2 Assembly Manual v0.95: correct hardware counting in p.30 and a typo in p.45.
2020-08-01 Update Assembly Guides for frame setup A and B.
    [SK-Go2 assembly guide - Setup A.stl, SK-Go2 assembly guide - Setup B.stl]
2020-08-02 SK-Go2 Assembly Manual: align Z rails to the bottom and flip bed supports (p.48, p.49)
2020-08-02 Add optional optical endstop mounts at XY min. positions
    [X optical endstop mount.stl, X optical endstop trigger.stl, Y optical endstop mount.stl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]
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2020-08-04 Add step file of Lerdge optical endstop.
    [Lerdge optical switch.step]
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2020-08-10 Update Y & X optical endstop mounts and instructions in README.md. Home Y to Max first, and then X min.
    [X optical endstop mount.stl, X optical endstop trigger.stl, Y optical endstop mount.stl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]
2020-08-11 Correct a wrongly uploaded STL of X min optical endstop mount
    [X optical endstop mount.stl]
2020-08-11 Correct a wrongly uploaded STL for Y optical endstop trigger finger
    [Y optical endstop trigger.stl]
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2020-08-21 SK-Go2 Assembly Manual v1.00: (p.25) Correct orientations of aluminum triangle brackets.
2020-08-21 Add printed parts for Belted-Z.
    [Belted-Z left belt clamp base.stl, Belted-Z right belt clamp base.stl, Belted-Z stepper mount.stl]
2020-08-26 SK-Go2 Assembly Manual v1.01: add more detailed description about swapping wire sequence to reverse stepper rotation direction.
2020-08-26 Separate and relocate different versions of belt clamp bases for SK-Go1 and SK-Go2.
    [Belted-Z left belt clamp base.SK-Go1.stl, Belted-Z left belt clamp base.SK-Go2.stl, Belted-Z right belt clamp base.SK-Go1.stl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]
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2020-10-11 SK-Go2 Assembly Manual v1.06: (A) Linear blocks and rails are now installed and cleaned as in p.5. (B) add links to non-included printed parts. (C) add a photo of NEMA17 stepper mount in p.52. (D) Re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
2020-11-17 update Belted-Z stepper mount to a correct, taller version.
    [Belted-Z stepper mount.stl]
2020-11-19 Assembly Manual v1.09: correct a type in p.76. Should be 5cm grounding wire, not 15cm.
2020-11-19 A stronger stepper mount for Belted-Z which avoids interference with the nearby bearing mount.
    [Belted-Z stepper mount.stl]
2020-11-19 Relocate Belted-Z stepper mount.
    [Belted-Z stepper mount.stl]
2021-01-04 add an unofficial Klipper config file
    [printer.cfg]
2021-01-15 Add STEP file of SK-Go/SK-Mini extruder plate and carriage.
    [SK-Go extruder carriage plates.step]
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2021-04-22 Add drawings of SK-Go back panel
    [SK-Go back panel Z350.dxf, SK-Go2 back panel Z350.dxf]
2021-08-01 add SD card contents of RepRap Firmware
    [bed.g, config.g, heightmap.csv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]
2021-08-01 arrange directory contents and add an all-in-one zip file
    [bed.g, config.g, heightmap.csv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]
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2022-02-12 Add Klipper config file for BTT Octopus by Jeffery Kilgore.
    [OctopusV1.1_Klipper_SKGo_TripleZ_BLTouch_Servo42C.cfg]
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2022-07-15 upload the step file of Belted-Z stepper mount
    [Belted-Z stepper mount.step]
2022-10-26 relocate Go2 related files to the new directory
    [12864 display cover with slope.stl, 12864 display cover.stl, 12864 display dial.stl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]
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2022-12-10 add STEP/STL files of the extruder carriage and bed
    [CF BMG adaptor.step, CF BMG adaptor.stl, CF XY belt clamp.step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]
2022-12-12 add a spacer to be inserted between a leadscrew nut and a Wobble Wafer.
    [lead screw nut spacer for Wobble Wafer.stl]
2023-06-06 Add files via upload
    upload a wider version of DXF file of the X plate.
    [Go1 X plate - wider.dxf]
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2024-05-12 Release the STEP files of frame, gantry and Z brackets.
    [Frame mockup.step, Gantry mockup.step, Z-bracket mockup mirror.step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]
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
